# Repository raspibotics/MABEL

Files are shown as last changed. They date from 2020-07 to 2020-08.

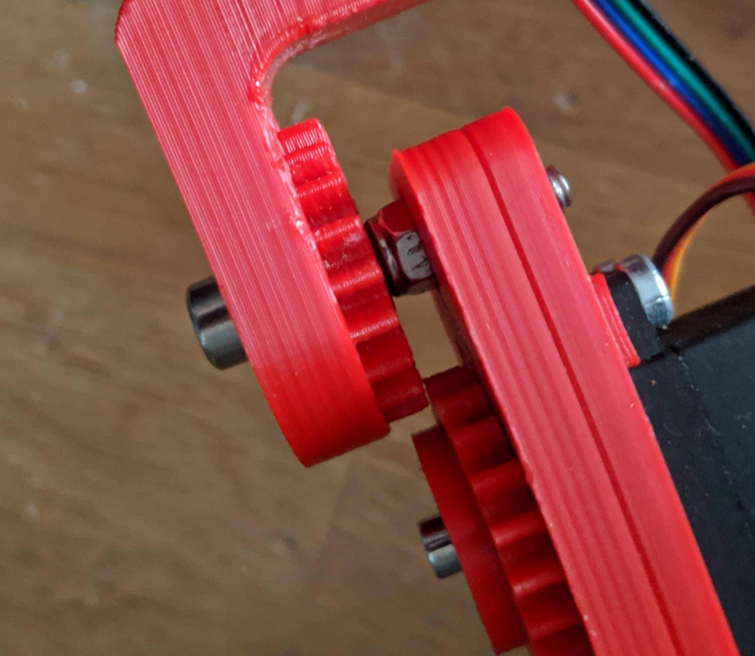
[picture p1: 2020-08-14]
docs/images/Mech_Step_1/Step_1(3).jpeg

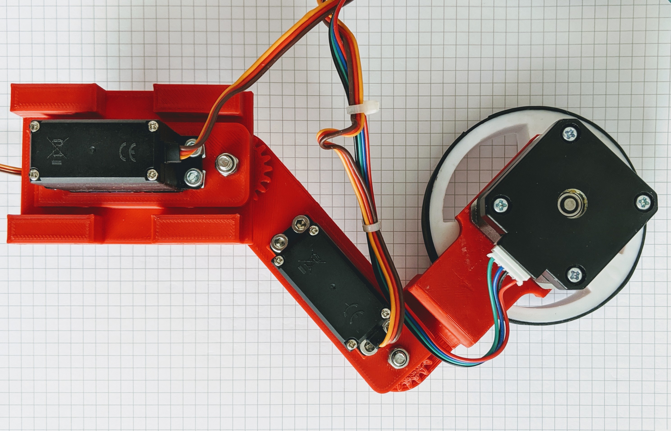
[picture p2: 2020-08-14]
docs/images/Mech_Step_5/Mech_Step_5.jpg

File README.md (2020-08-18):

# MABEL (Multi Axis Balancer Electronically Levelled)
MABEL
## Table of contents
 - [About MABEL](#about-mabel)
   - [Features and design](#features-and-design)
 - [Bill of Materials (BOM)](#bill-of-materials)
   - [3D Printable](#3d-printable)
   - [Non 3D Printable](#non-3d-printable)
     - [Electronic components](#electronic-components)
     - [Mechcanical components](#mechanical-components)
 - [Build instructions](#build-instructions)
     - [Mechanical assembly](#mechanical-assembly)
     - [Electronics assembly](#electronics-assembly)
 - [Installation](#installation)
     - [Dependencies](#required-librariesdependencies)
 - [Usage](#usage)
     - [Inverse kinematics - Moving the legs](#iksolve---inverse-kinematics-for-mabel)
     - [Driving controls and serial communication](#driving-controls)
 - [Contact/Support](#contactsupport)

## About MABEL
**MABEL** is an **ongoing** open source self balancing robot project that is inspired by the famous [Boston Dynamics Handle robot](https://www.youtube.com/watch?v=-7xvqQeoA8c "Boston Dynamics Handle robot"). The robot is controlled via an **Arduino** that handles all of the PID calculations (based off of open source [YABR](http://www.brokking.net/yabr_main.html " YABR") firmware) based on the angle received from an MPU-6050 Accelerometer/Gyro, whilst a **Raspberry pi** (code in **python**) manages Bluetooth and servo control, running an inverse kinematics algorithm to translate the robot legs perfectly in two axes.

> The goal of **MABEL** is to create an affordable legged balancing robot platform like the the Boston Dynamics Handle robot that can built on a hobby scale using cheap Amazon parts and components.

By having a balancing platform with articulated legs **MABEL** will be able to actively balance in multiple Axes and vary leg length depending on the surroundings to increase terrain and off-road performance.

**MABEL** has built on the open source [YABR](http://www.brokking.net/yabr_main.html "YABR") project for the PID controller but with the addition of servos and a pi that helps interface them and control everything.
### Features and design 
Some of the stand-out features that make **MABEL** different from other balancing robots are:
- **Movable Legs** (**Enhanced mobility**, **terrain** and **stabilisation** capabilities)
- **Inverse Kinematics** for each legs that enables accurate translation in (x, y) coordinates using the [IKSolve.py](https://github.com/raspibotics/MABEL/blob/master/raspi_code/IKSolve.py) class
- **Raspberry Pi** enabled (for **Bluetooth control**, **wireless connectivity** and **Computer Vision** capabilities)
- **Common/cheap build materials** (All of the materials can be purchased off of Amazon/Ebay for a low cost)
- **Stepper Motors** (Accurate positioning and precise control)

## Bill of materials
### 3D Printable
3D Printable files are found in [/CAD/3D Models (To Print)](https://github.com/raspibotics/MABEL/tree/master/CAD/3D%20Models%20(To%20print))
- [BatteryPack](https://github.com/raspibotics/MABEL/blob/master/CAD/3D%20Models%20(To%20print)/BatteryPack.stl) (**Optional** - holds LiPo battery onto back of robot with M5 Bolts)
- **2x** [BodyPanel](https://github.com/raspibotics/MABEL/blob/master/CAD/3D%20Models%20(To%20print)/BodyPanel.stl) (Mounting for the 'Hip' servos and side panels of the body)
- [BodyTop](https://github.com/raspibotics/MABEL/blob/master/CAD/3D%20Models%20(To%20print)/BodyTop.stl)
- **4x** [DriverGear](https://github.com/raspibotics/MABEL/blob/master/CAD/3D%20Models%20(To%20print)/DriverGear.stl)
- [Housing](https://github.com/raspibotics/MABEL/blob/master/CAD/3D%20Models%20(To%20print)/Housing.stl) (**LOWER** body housing for MABEL)
- **2x** [LowerLeg](https://github.com/raspibotics/MABEL/blob/master/CAD/3D%20Models%20(To%20print)/LowerLeg.stl)
- **2x** [UpperLeg](https://github.com/raspibotics/MABEL/blob/master/CAD/3D%20Models%20(To%20print)/UpperLeg.stl)
- [PanBracketHead](https://github.com/raspibotics/MABEL/blob/master/CAD/3D%20Models%20(To%20print)/PanBracketHead.stl) (**Optional** Pan servo bracket for head assembly)
- [TiltBracketHead](https://github.com/raspibotics/MABEL/blob/master/CAD/3D%20Models%20(To%20print)/TiltBracketHead.stl) (**Optional** Tilt servo bracket for head assembly)
- [UpperBody](https://github.com/raspibotics/MABEL/blob/master/CAD/3D%20Models%20(To%20print)/UpperBody.stl) (**UPPER** body housing for MABEL)
- **2x** [Wheel](https://github.com/raspibotics/MABEL/blob/master/CAD/3D%20Models%20(To%20print)/Wheel.stl) (**Optional** You can 3D Print your own set of wheels, or buy wheels)

### Non 3D Printable
Here are the Non 3D printable materials to build **MABEL** that **must be either purchased or sourced**. **This includes all of the electronics, mechanical hardware and fixings.** It is **recommended to overbuy the nuts and bolts fixings, as the exact number can change between builds.** This [amazon list](https://www.amazon.co.uk/gp/registry/wishlist/1K7SOU8MRG2K7/ref=cm_wl_huc_view) contains a rough idea of what needs to be purchased.

### Electronic components
- **Raspberry Pi** Zero W
- **PCA9865** Servo Controller (A **PiconZero** could, and previously was used)
- **Variable voltage regulator** (**Optionally** 2x regulator to supply servos with a higher voltage than the 5V required for the  pi)
- **Arduino** Uno 
- **6x** MG996R metal gear servos
- **2x** 38mm NEMA17 stepper motors
- **2x** A4988 (or **DRV8825**) stepper motor drivers 
- Arduino CNC Shield
- MPU-6050 gyro/accelerometer
- 11.1V 2800mAh 3S LiPo (**LiPo battery charger is required**)

### Mechanical components
- **Optional** Grippy rubber material for tyre tread if you are using the [Wheel](https://github.com/raspibotics/MABEL/blob/master/CAD/3D%20Models%20(To%20print)/Wheel.stl) provided.
- **6x** Aluminium servo horns (for **MG996R** servos)
- **8x** 	10mm diameter bearings (5mm internal diameter) x 4mm depth 
- **12x** 10mm M3 bolts
- **12** 15mm M5 bolts
- **4x** 30mm M5 bolts
- **16x** 15mm M4 bolts
- **20x** M5 locknuts and washers

## Build instructions
***UNDER CONSTRUCTION**: This section will include:*
- *Recommended 3D printer settings for 3D Printable parts*
- *Mechanical assembly instructions*
- *Electronics/Wiring instructions*

## Mechanical assembly
---

### **Step 1:** Press the bearings into the joints 
push fit the bearings and secure with a nut and bolt Push fit bearings

 Each leg section ([UpperLeg](https://github.com/raspibotics/MABEL/blob/master/CAD/3D%20Models%20(To%20print)/UpperLeg.stl)  and [LowerLeg](https://github.com/raspibotics/MABEL/blob/master/CAD/3D%20Models%20(To%20print)/LowerLeg.stl)) requires **two bearings (thats 8x bearings in total) to push fit on opposing sides** to ensure smooth rotation. The bearings can be quite tricky to fit so it's **advisable to either apply slow, even pressure with a bench vice**, or to **soften the plastic with a hairdryer** to make it easier to push in by hand. Once you've fitted the bearings, you need to **push an M5 (**4x in total**) (30mm) bolt through** the hole left and **secure with a locknut**.
 [*More reference images for Step 1*](https://github.com/raspibotics/MABEL/tree/master/docs/images/Mech_Step_1)

---

### **Step 2:** Attach **4x** Servos to the [UpperLeg](https://github.com/raspibotics/MABEL/blob/master/CAD/3D%20Models%20(To%20print)/UpperLeg.stl)(s)and [BodyPanel](https://github.com/raspibotics/MABEL/blob/master/CAD/3D%20Models%20(To%20print)/BodyPanel.stl)(s) using **M4 (15mm)** bolts 
Attach servos with M4 bolt Attach servos

**4x MG996R servos** must be secured to **2x BodyPanel and 2x UpperLeg** using **4x M4 (15mm) bolts (16x in total)**. The servos **must sit flat** against these parts with the **shaft facing towards the outside of the robot**. *Your **servos may have a small rib** that you can **easily sand or file off** to get the servo to sit in this orientation.* [*More reference images for Step 2*](https://github.com/raspibotics/MABEL/tree/master/docs/images/Mech_Step_2)

---

### **Step 3:** Push fit and screw the **servo horns** into the [DriverGear](https://github.com/raspibotics/MABEL/blob/master/CAD/3D%20Models%20(To%20print)/DriverGear.stl)(s) and attach the assemblies to the servos 
push fit servo horns and attach gear to servo Assemble DriverGear

Take your **4x DriverGear parts** and **4x Aluminium Servo horns** and push it into the recess on the bottom of the gear. Then **secure the servo horns to each of the gears using the screws** that (should) come with servo horns. Once the gear assembly has been completed, screw it on to the **servo shaft** using **one M3 (10mm) bolt per servo**. [*More reference images for Step 3*](https://github.com/raspibotics/MABEL/tree/master/docs/images/Mech_Step_3)

---

### **Step 4:** Attach the NEMA17 Motors to the [LowerLeg](https://github.com/raspibotics/MABEL/blob/master/CAD/3D%20Models%20(To%20print)/LowerLeg.stl) and fit the wheels
push fit wheels, attach motors Fit wheels and motors

Secure one **NEMA17** (**2x in total**) stepper motor to each of your (**2x**) [LowerLeg](https://github.com/raspibotics/MABEL/blob/master/CAD/3D%20Models%20(To%20print)/LowerLeg.stl) parts with **4x M3 (10mm)** bolts (**8x in total**). Next, prepare your wheels and then **push fit** onto the NEMA17 shafts, **securing if necessary with an M4 bolt**:
- If you are **using the included** [Wheel](https://github.com/raspibotics/MABEL/blob/master/CAD/3D%20Models%20(To%20print)/Wheel.stl) part, you will **need to wrap the outside** in a thin layer of **grippy material** such as **elastic bands** or in my case, **rubber 'O' rings** which help create **traction**.
- If you've **sourced your own wheels**, insert them onto the NEMA17 shafts, and secure as necessary. 

[*More reference images for Step 4*](https://github.com/raspibotics/MABEL/tree/master/docs/images/Mech_Step_4)

---

### **Step 5:** Attach the [LowerLeg](https://github.com/raspibotics/MABEL/blob/master/CAD/3D%20Models%20(To%20print)/LowerLeg.stl), [UpperLeg](https://github.com/raspibotics/MABEL/blob/master/CAD/3D%20Models%20(To%20print)/UpperLeg.stl) and [BodyPanel](https://github.com/raspibotics/MABEL/blob/master/CAD/3D%20Models%20(To%20print)/BodyPanel.stl) assemblies together using **4x M5 locknuts**

Attach all assemblies so far together Fit everything together

Now that you have fitted the BodyPanel and UpperLeg parts with servos (**Step 2**) and gears (**Step 3**), and prepared the UpperLeg and LowerLeg sections with bearings, an M5 bolt and a lock nut each (**Step 1**), you can **insert the UpperLeg section into the BodyPanel** and **secure it with a locknut** on the back (servo) side. Then, **secure the LowerLeg assembly to the UpperLeg** assembly with another **M5 locknut** to form one leg. **This step should then be repeated for the side.** 

**NOTE:** When fitting the parts together, **special attention** should be considered to the **position of the servo rotors**. With standard 180 degree servos, full range of motion is only possible with one way of the legs being bent (The minimum leg height requires a greater than 90 degree angle for example) - **decide which way the legs should bend out** and turn the servo gear manually by hand to **allow a greater range of motion in that direction** than the other (it will be opposite because of the gear drive). You will then **calibrate the servos later on** with a new 0 **position** that's needed for the legs to work properly.

[*More reference images for Step 5*](https://github.com/raspibotics/MABEL/tree/master/docs/images/Mech_Step_5)

---
## Electronics Assembly
***This section will contain instructions about the construction of the robot electronics***

---
## Installation
### Required Libraries/Dependencies
The **MABEL** project relies on multiple open-source and independent libraries, whilst MABELs own classses and functions may run natively, certain libraries are required for full functionality.

- Adafruit ServoKit PCA9865 servo controller library - [Installation guide](https://learn.adafruit.com/adafruit-16-channel-servo-driver-with-raspberry-pi/overview)
- python3 Cwiid (**Optional** - If you want to use a Wiimote controller) - [Installation guide](https://automaticaddison.com/how-to-make-a-remote-controlled-robot-using-raspberry-pi/)
- [approxeng.input](https://approxeng.github.io/approxeng.input/) (**Optional** - If you want to use a different controller - **recommended**)
  
***The controller code is still under development, however the approxeng.input library is recommended to develop controller code with - Versions for both the approxeng.input libary and Cwiid will be released eventually.***

Aftere following the installation instructions for the [ServoKit](https://learn.adafruit.com/adafruit-16-channel-servo-driver-with-raspberry-pi/overview) and controller library of your choice, you should be able to clone to the Raspberry Pi with `git clone https://www.github.com/raspibotics/MABEL`, all controller code, and other scripts should be written in the [MABEL/raspi_code/](https://github.com/raspibotics/MABEL/tree/master/raspi_code) directory so that the code will be able to reference the code already included.

## Usage 
### IKSolve - (Inverse Kinematics for MABEL)
**IKSolve** is the class that handles the **inverse kinematics** functionality for **MABEL** [(IKSolve.py)](https://github.com/raspibotics/MABEL/blob/master/raspi_code/IKSolve.py) and allows for the legs to be translated using **(x, y)** coordinates. It's really simple to use, all that you need to specify are the **home values of each servo** (these are the angles that when passed over to your servos, make the legs point **directly and straight downwards** at **90 degrees**). Keep in mind that the values below are just my servo home positions, and **yours will be different**. 
 
 *The code below is taken directly from [IKDemo.py](https://github.com/raspibotics/MABEL/blob/master/raspi_code/IKDemo.py)*

```python
from IKSolve import IKSolve

# Servo Home Values (degrees) - ***YOURS WILL DIFFER***
# ru_home = 50   # Right leg upper joint home position (servo_angle[0])
# rl_home = 109   # Right leg lower joint home position (servo_angle[1])
# lu_home = 52   # Left leg upper joint home position (servo_angle[2])
# ll_home = 23   # Left leg lower joint home position (servo_angle[3])
 
ik_handler = IKSolve(ru_home=50, rl_home=109,  # Pass home positions to IK class
                     lu_home=52, ll_home=23)  
```
***The class can also be initialised with different leg length segments but these are best left to default unless you have changed the length of any of the leg components.***
```python
def __init__(self, ru_home, rl_home, lu_home,  
                 ll_home, upper_leg=92, lower_leg=75):
```
To recieve suitable angles for each servo to move to (x, y) you must use `translate_xy(self, x, y, flip=False)` (Flip inverts the direction that the legs bend, by default this should be set **False**)

- **x translates the robot leg vertically and y translates the leg horizontally**, each value should be in integer mm
  
 - **x is the distance between the upper leg pivot and wheel centre** (Vertically) - acceptable range for MABEL (160-98mm)
  
 - **y is the distance between the upper leg pivot and wheel centre** (Horizontally) - acceptable range for MABEL (-50, 50mm)
 
```python
  x = int(input('x:'))
  y = int(input('y:'))
  servo_angle = ik_handler.translate_xy(x, y, flip=False) 
  # The angles calculated are stored in a tuple E.g. servo_angles[0-3]
  # You can pass these values to your servo controller code
```
Here are the **mathematical equations** that were calculated for MABELs inverse kinematics, and are expressed in the ```translate_xy()``` function in IKSolve. A is used for calculating angles for the top servos (mounted to the BodyPanel) B is used to calculate angles for the 'Knee' servos. ***Upper*** represents the distance of the **UpperLeg** from pivot to pivot and ***lower*** represents the distance between the **LowerLeg** pivot and centre of the wheel (motor shaft).

<a href="https://github.com/raspibotics/MABEL/blob/master/docs/IKSolve/IKSolveFormulaForA.png" target="_blank">A = Cos^{-1}(\frac{upper^{2}+x^{2}-lower^{2}}{2\cdot upper\cdot x}) + Tan^{-1}(\frac{y}{x})</a>

<a href="https://github.com/raspibotics/MABEL/blob/master/docs/IKSolve/IKSolveFormulaForB.png" target="_blank">B = Cos^{-1}(\frac{upper^{2}+lower^{2}-(x^{2}+y^{2})}{2\cdot upper\cdot lower})</a>
### Driving controls
**MABEL** is designed to work by listening to commands on the Arduino (PID contoller) end that are sent to it by the raspberry pi over serial (using [pySerial](https://pyserial.readthedocs.io/en/latest/)). This allows easy control using bluetooth and web based solutions that are much more difficult to get working on an Arduino. The code snippets below show how you could modify/write your own controller code by sending specific bytes over serial to the arduino and [YABR](http://www.brokking.net/yabr_main.html) based firmware.

In order to use serial commands to drive MABEL around, you first need to find what serial port that the USB connection between the raspberry pi and arduino is called. In my case it was ```/dev/ttyACM0``` but yours could be different. To find what serial port your arduino is connected to, type ```ls /dev/tty*``` into the terminal **without the arduino connected**. Then **reconnect the arduino**, run ```ls /dev/tty*``` again, and make a note of which serial port appears to be listed that was not previously there - **this is your serial port.**

*Once you know what serial port the arduino is connected on, you should initialise the serial class with it:*
```python
import serial
from struct import pack
from time import sleep

ser = serial.Serial(port='/dev/ttyACM0', # ls /dev/tty* to find your port
		baudrate = 9600,
		parity = serial.PARITY_NONE,
		stopbits = serial.STOPBITS_ONE,
		bytesize = serial.EIGHTBITS,
		timeout = 1)
```
The YABR code on the arduino accepts bytes [0, 1, 2, 4, 8] as driving input commands, with **0b00000000 being 'No movement/ remain stationary'**:
```python
# sendByte code
# 00000000 - Do nothing
# 00000001 - Turn left
# 00000010 - Turn right
# 00000100 - Move forwards
# 00001000 - Move backwards
```
We can then send these bytes over the serial connection, and tell **MABEL** in which direction to move - Here's an example of how to write to the arduino serial port, with a bit of **controller pseudocode** for clarity:
```python
while True:
    sendByte |= 0b00000000 
    if controller.direction == 'LEFT': # Controller pseudocode 
        sendByte |= 0b00000001 # This could be any sendByte
    val = pack("B", sendByte)
    ser.write(val) # Send the value over to the arduino 
    sleep(0.04) # Sleep for this period before sending next command
```

## Contact/Support
Thanks for taking an interest in MABEL and its development! If you have any questions or need information whilst building MABEL, please feel free to mention me on twitter [@raspibotics](https://twitter.com/raspibotics) or send me an email at **raspibotics@gmail.com**. ***Whilst this page is still undergoing development, you can find updates and more information on my blog [https://raspibotics.wixsite.com/pibotics-blog](https://raspibotics.wixsite.com/pibotics-blog), where I have been posting about the development of MABEL.***

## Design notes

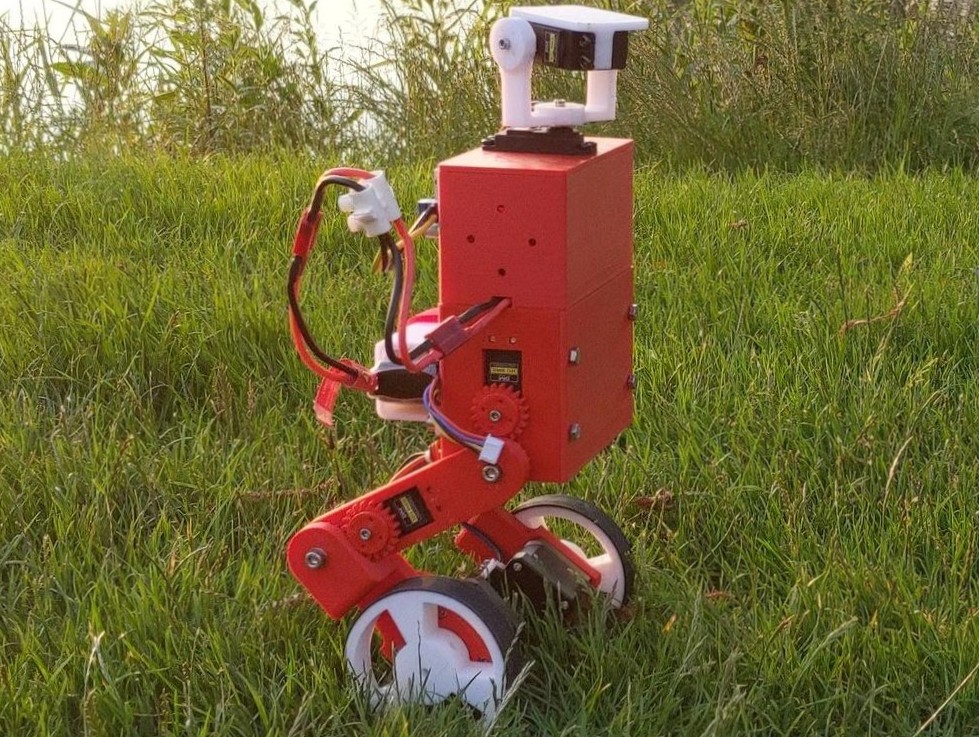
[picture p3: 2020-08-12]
docs/images/MABEL.jpeg

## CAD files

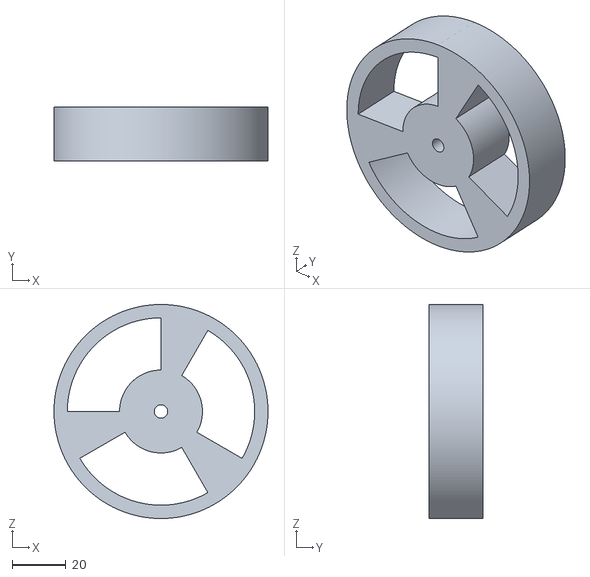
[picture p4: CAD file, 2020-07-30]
CAD/3D Models (To print)/Wheel.stl
80.0 x 20.0 x 80.0

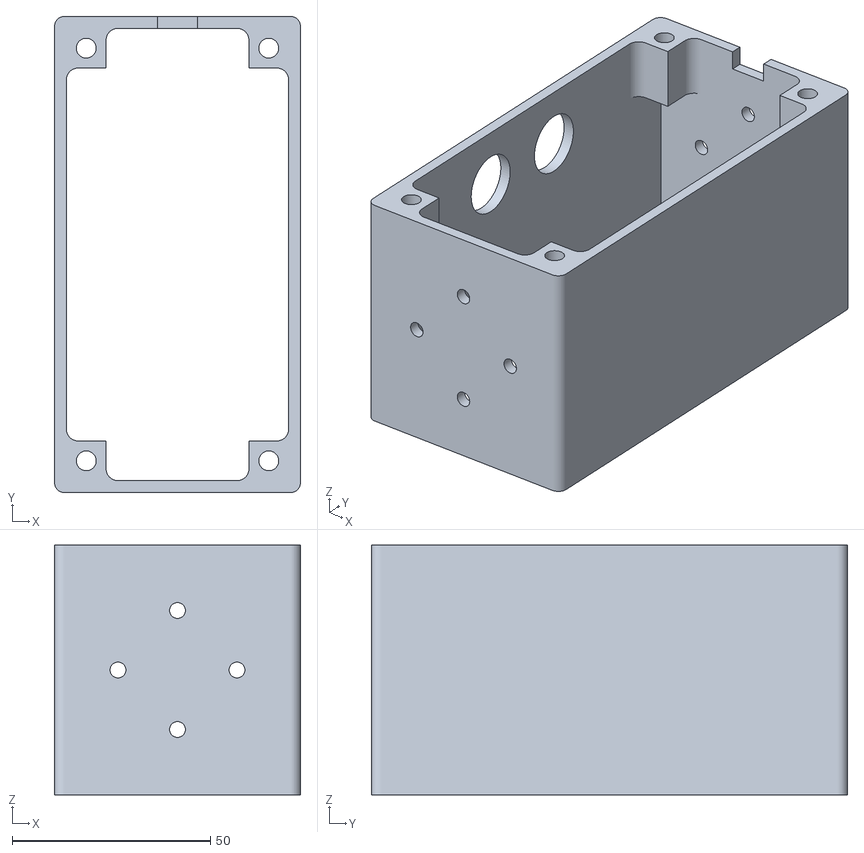
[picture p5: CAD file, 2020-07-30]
CAD/3D Models (To print)/UpperBody.stl
62.0 x 120.0 x 63.0

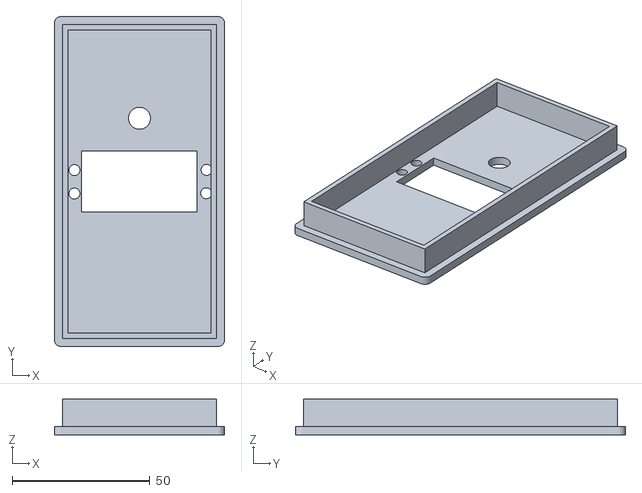
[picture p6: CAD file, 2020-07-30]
CAD/3D Models (To print)/BodyTop.stl
62.0 x 120.0 x 13.0

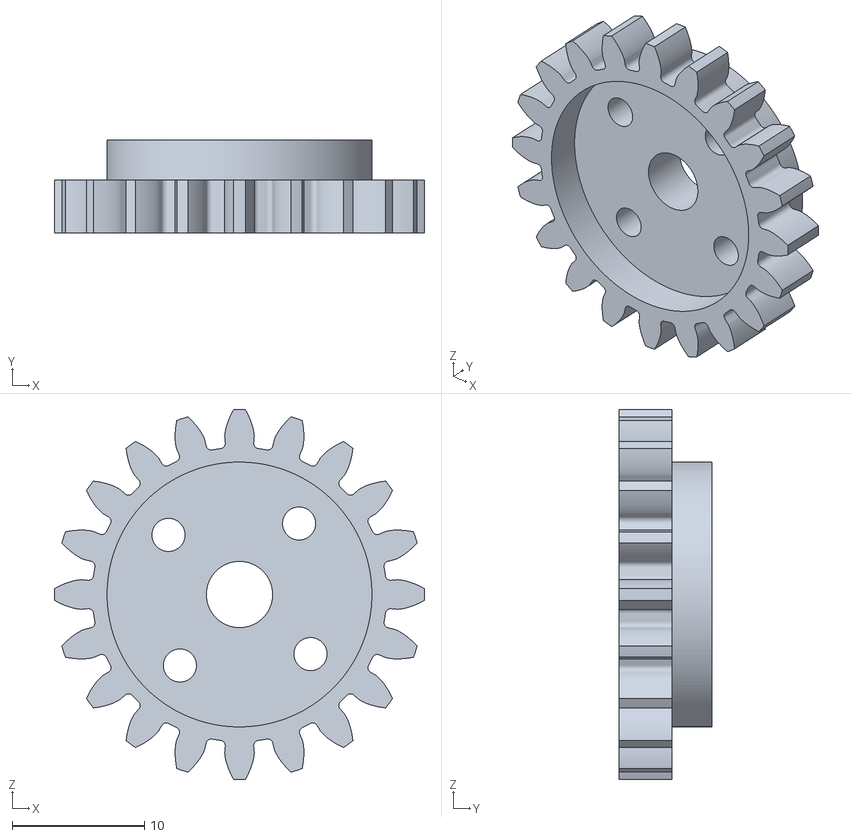
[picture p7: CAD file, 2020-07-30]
CAD/3D Models (To print)/DriverGear.stl
27.9 x 7.00 x 27.9

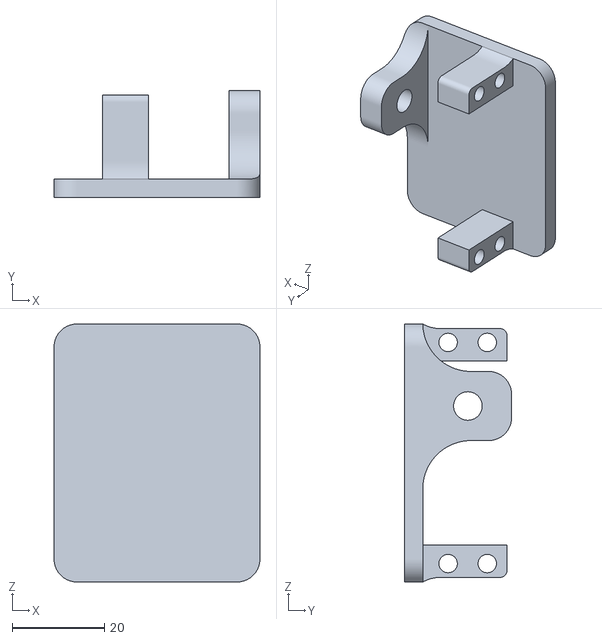
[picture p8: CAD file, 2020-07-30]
CAD/3D Models (To print)/TiltBracketHead.stl
44.7 x 23.3 x 56.0

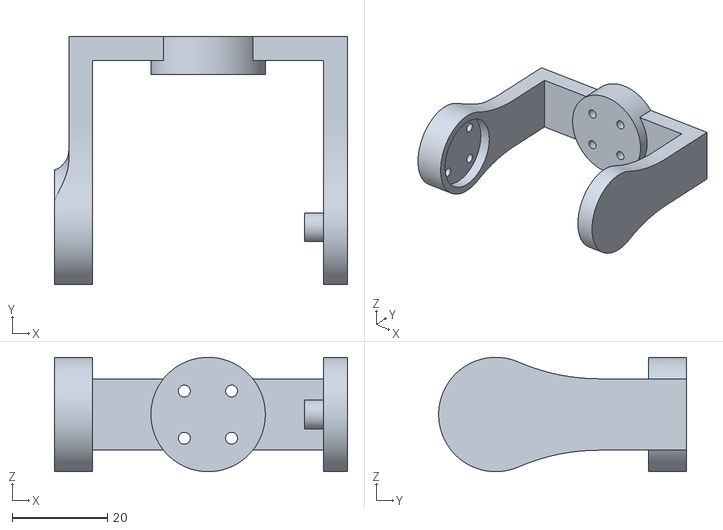
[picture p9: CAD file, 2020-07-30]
CAD/3D Models (To print)/PanBracketHead.stl
61.5 x 52.0 x 24.0

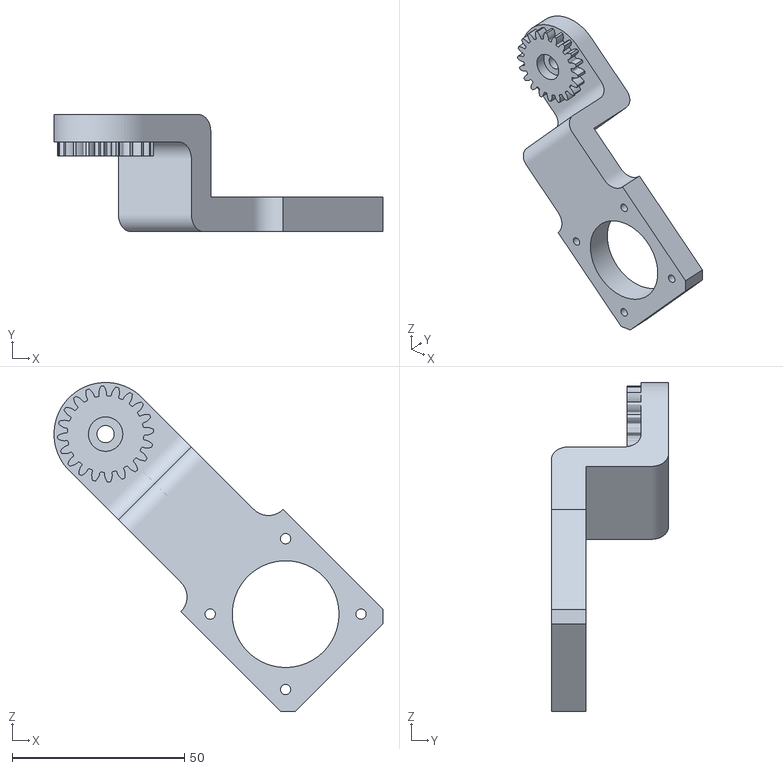
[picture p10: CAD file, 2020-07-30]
CAD/3D Models (To print)/LowerLeg.stl
95.6 x 34.0 x 95.6

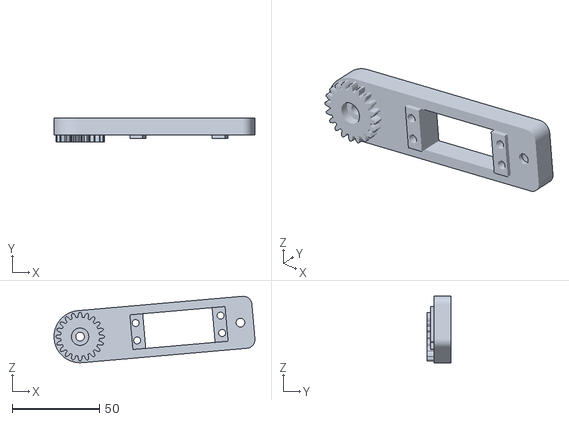
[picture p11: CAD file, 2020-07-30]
CAD/3D Models (To print)/UpperLeg.stl
115.5 x 14.0 x 38.2

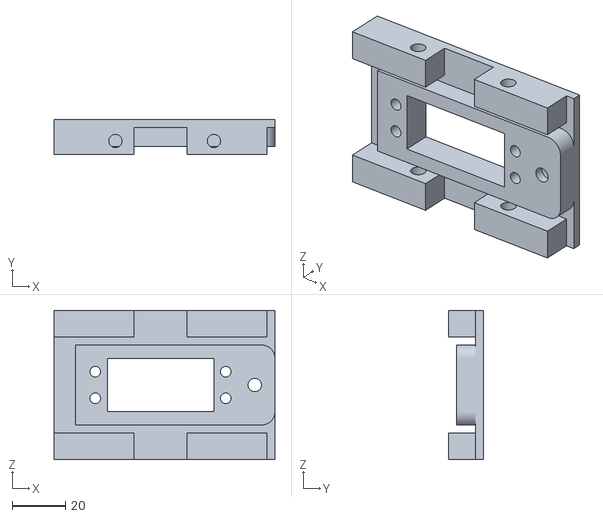
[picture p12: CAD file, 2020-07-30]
CAD/3D Models (To print)/BodyPanel.stl
83.0 x 13.0 x 56.0

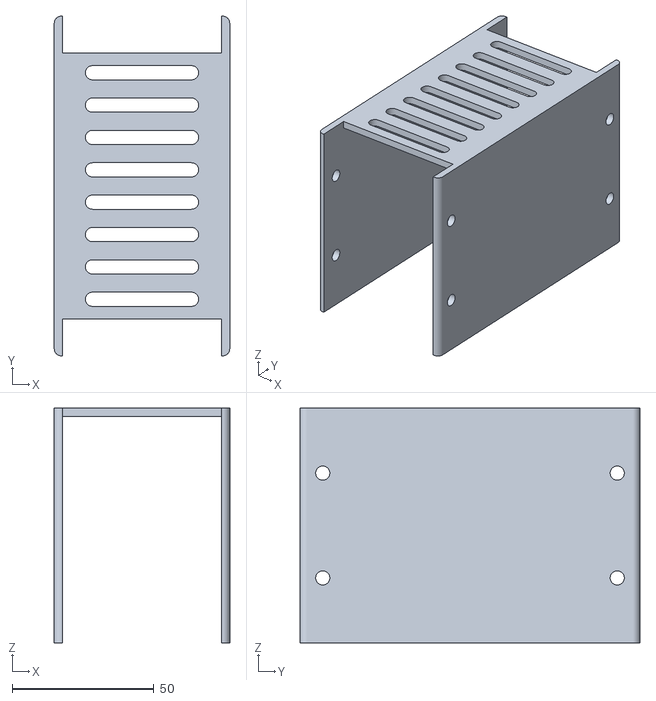
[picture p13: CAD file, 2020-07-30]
CAD/3D Models (To print)/Housing.stl
62.0 x 120.0 x 83.0

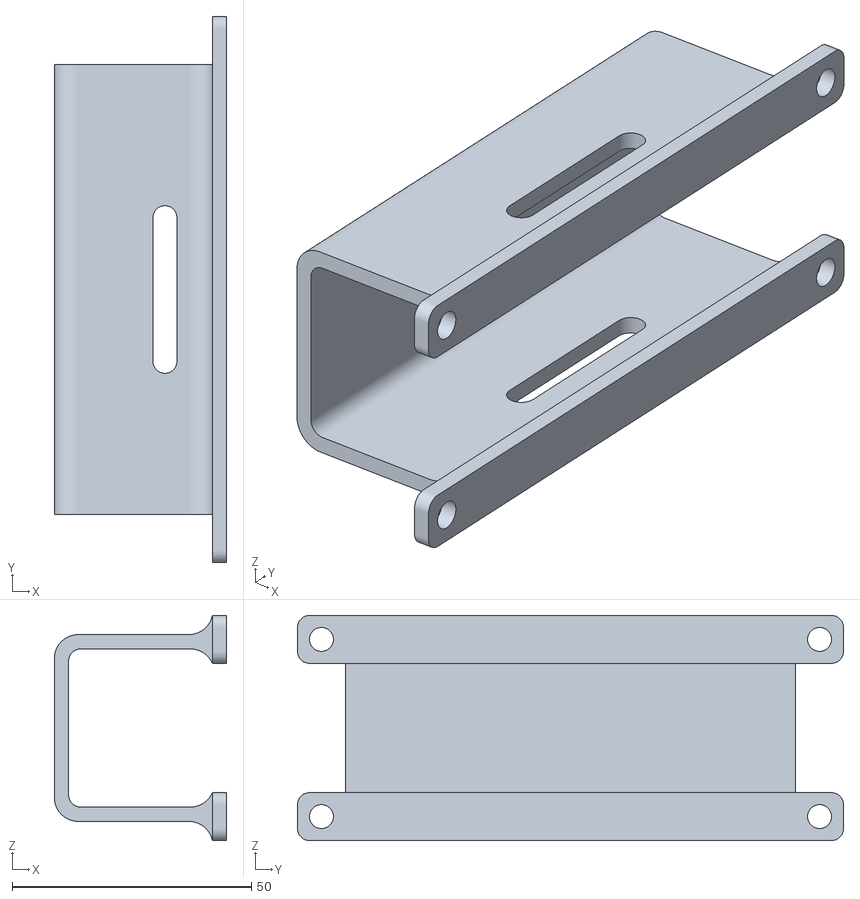
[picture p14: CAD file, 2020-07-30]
CAD/3D Models (To print)/BatteryPack.stl
36.0 x 114.0 x 47.0

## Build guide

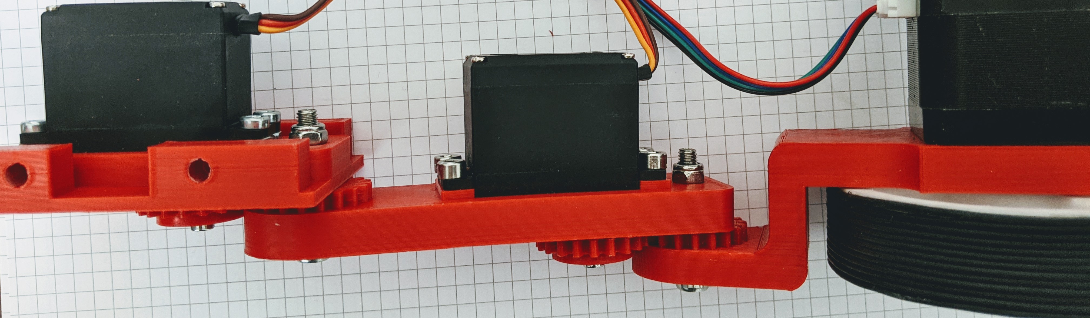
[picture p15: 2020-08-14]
docs/images/Mech_Step_5/Mech_Step_5_side_view.jpg

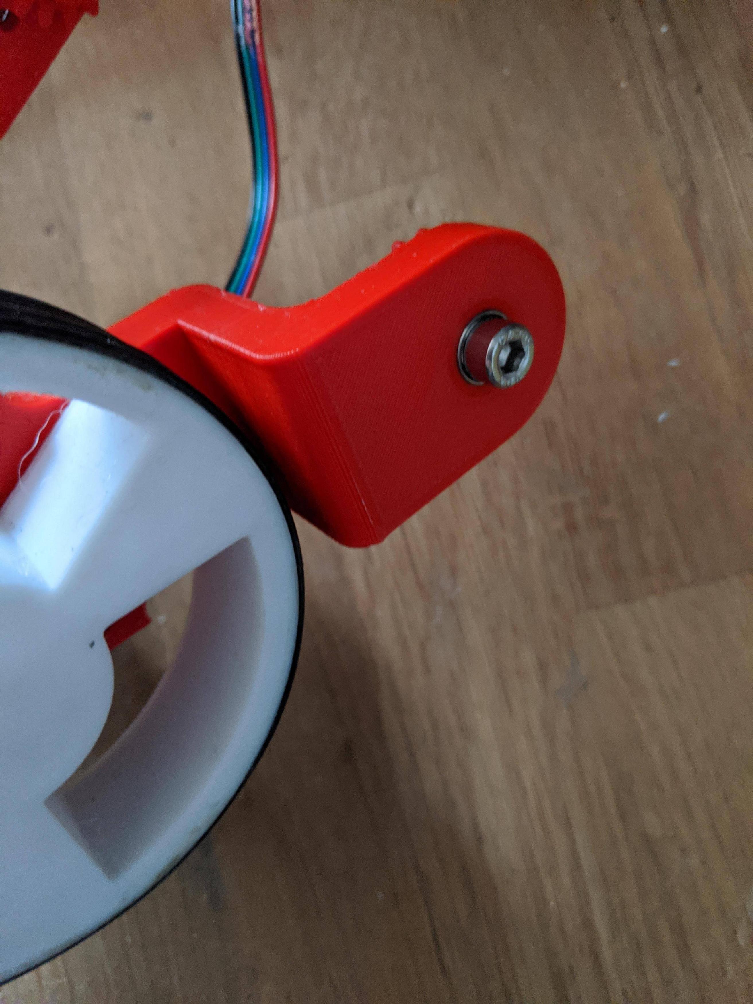
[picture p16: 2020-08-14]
docs/images/Mech_Step_1/Step_1(2).jpeg

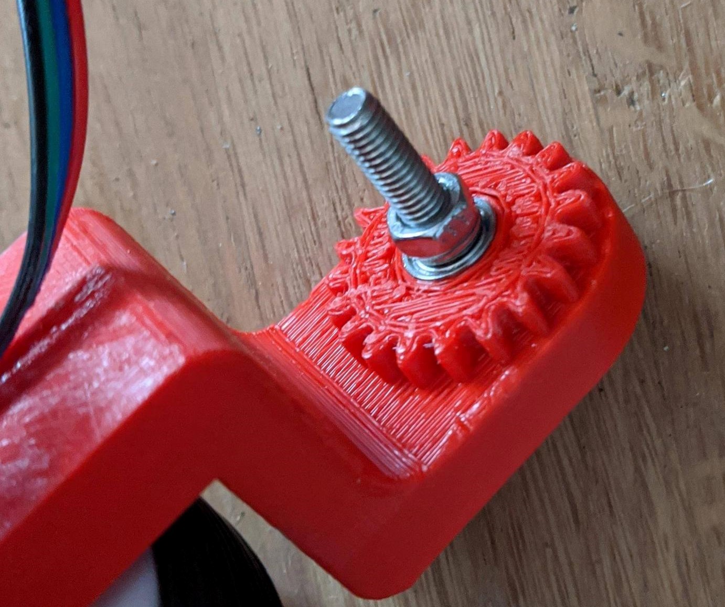
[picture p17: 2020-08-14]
docs/images/Mech_Step_1/Step_1(1).jpeg

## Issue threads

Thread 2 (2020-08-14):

Typo in parts list?

carlkesselman, 2020-08-14:
Hi,

I think there may be a type in the parts list: PCA9865 -> PCA9685?

It's a bit confusing as it seems you have changed from the Picon Zero to this alternative, which I assume will still be controlled from the Pi, not the Arduino?

Carl

raspibotics, 2020-08-14:
Hi,
I've recently switched over to the PCA9865 servo controller on the pi as it's cheaper and more suited to my robot application, although a Piconzero is still a valid servo controller for the Pi.

raspibotics, 2020-08-15:
Updated parts list with (PiconZero could, and previously was used)

Closed 2020-08-15.

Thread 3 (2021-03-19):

Can't get YABR code running on Arduino Uno + CNC Shield

ghost, 2021-03-19:
Hey there,
I'm having some issues getting the YABR code working. I've got the same hardware as mentioned in your project. An Arduino Uno (SMD version, should not differ, as far as I researched) and CNC Shield. It seems the code fails on following line:
`TIMSK2 |= (1 << OCIE2A);`
The result of running the YABR code are two non functional stepper motors. One of them can be moved by hand, the other one being blocked at a position. Both are producing some noise. I checked the current limit on the driver and used other motor drivers. Unfortunately without success.

I tried to increase `OCR2A = 39;` to `3999999` which should result in a timer interrupt every 2 seconds instead the 20 µs, but looking into serial output the timer would still spam the code, way faster than 2 seconds.
I replaced the Arduino with another one (different brand, same processor, not SMD). Same behavior there.
I replaced the writing to `PORTD` with `digitalWrite()` but had no luck either.

Could it be possible that I'm missing out on some point not mentioned in the guide?

Greetings,
Niko

raspibotics, 2021-03-19:
Hi Niko,

I had issues at first with getting my steppers to cooperate. I would
suggest testing some seperate example code to see if you can get any sort
of movement out. Are you absolutely sure that you've wired the correct
stepper coils to the stepper drivers? I know when I did the guide I was
following had some inaccuracies so I had to use trial and error as well as
measuring the resistance to determine which order the coils should be
connected. If they are connected wrong the stepper will move unexpectedly
or lock up but when working correctly should activate when the
accelerometer reads the critical value.

There shouldn't be too many differences with board pinnout and I'm afraid I
can't help diagnose too many software issues with the original YABR code as
I left it mostly unchanged and did most of the software on the raspberry
pi. Although the original author goes through the code in great detail in
these two videos if you rule out hardware.

https://youtu.be/VxpMWncBKZc

https://youtu.be/mG4OtAiY_wU

Hope this helps,

Harry

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

niko-kl, 2021-03-21:
Hi Harry,

thanks for your fast response.
I forgot to mention that I succeeded in controlling the stepper motor with some separate test code, before I asked my first question.
After watching the two videos you linked I noticed that my driver was set to full instead of 1/4 step mode. Setting the jumper my robot started balancing or at least trying it. So the wheels are spinning now, but way to fast.. resulting in the robot falling over. When tilting the robot I can confirm that the wheels are changing their direction, but they are still spinning, even if I balance the robot manually by hand. Did you experience something similar?
Did also correct my MPU position to being equal to the balancing robot in the video. So I can exclude this being a part of the problem.

Current connections on the CNC board are:

- drivers, stepper motor, 1/4 step jumpers
- EN/GND jumper to enable the board
- power input for stepper motor
- MPU connection with SDA/SCL

Am I missing some jumpers?

Greetings,
Niko

raspibotics, 2021-03-21:
Hi!

When oriented like the original the MPU calibration value should be around
1000, once I had sorted out hardware issues the thing balanced pretty well
with no modifications to the PID values. My microstepping jumper is in the
second slot  to create a 1/4 step but where you place the jumper will
differ depending on the truth table for your particular driver. Are you
using A4988 drivers?

Could you send a video, it may help to see what's going on?  The wheels do
spin very fast in mid air but when angled slowly into position it should
just take over and begin balancing.

Harry

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

niko-kl, 2021-03-21:
Hey,

yes I'm using the A4988 driver, so my microstepping jumper is also set on the second slot.
Meanwhile I was able to find my problem. The stepper coils were indeed wired wrong. Fixing that the balancing part finally works.

I made still a [video](https://drive.google.com/file/d/13ucOEg1BF7VQoPmIf4q2sNA6-ISzJRO4/view?usp=sharing) for the (new) sound my stepper motors are producing when I'm lifting the robot. My best guess would be that the current limitation is set wrong. By looking into the datasheet, I read a motor needs 1.7A. So Vref on the driver should be half of that. But neither 0.85V nor less than tha (down to 0.5V) would fix this. Other than that I'd need to get another power adapter, since mine has 12V and only 2.5A, so I can exclude that as an issue.

Niko

raspibotics, 2021-03-21:
Hi!

Wow that's awesome, the Motors have a tendency to do that when they've
stalled, if you increase the motor current allowed this should solve that
although it will still stall in extreme cases, only thing you can do is to
tip the robot on its side which will reset the motors.  By the way us
mentioned setting the VREF to 0.85v for 1.7A, this would be correct for
DRV8825 drivers but for A4988 the formula used is slightly different and is
based on one of the SMD resistors.  This guide should help you set the
correct Vref but it may still stall in extreme cases.

https://e3d-online.dozuki.com/Guide/VREF+adjustment+A4988/92

Harry

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

niko-kl, 2021-03-24:
Hey there,

I guess I have the Stepstick or a clone driver since it's red colored. There is not datasheet available where I bought it.
Taking the information for Rs = 0,2 out of [here](https://v6zmvq5nk5.codesandbox.io/) and input there 1.7A as rated current I get 2.18V for Vref.. which is probably way to high and wrong. I tried to adjust the driver current to 1V and the motor began to get small pulses in idle, so I stopped there.
Adjusted the current just by trial and error and the best value for me seems to be around 0.4 to 0.5 for Vref. Then the motor doesn't even make any sounds in idle. I guess I stick to that solution for the beginning.

raspibotics, 2021-03-24:
Hi,

Yeah it's not a major issue, 1.7A does seem quite high however. I got
confused with stepper powering early on, the current drawn is dependent on
the voltage supplied to the motors, the motor datasheets tend to give a
high rated current but it will usually be at a low supply voltage maybe
around 3V. Since you're powering off I'm assuming around 12V the actual
current should be much lower and the driver current rating should match
that. So looking at rated power may be a more useful metric. Trial and
error will probably work though and you can always increase it later.

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

Closed 2023-09-21.

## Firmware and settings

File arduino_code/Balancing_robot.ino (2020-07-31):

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
#include <Wire.h>                                            //Include the Wire.h library so we can communicate with the gyro

int gyro_address = 0x68;                                     //MPU-6050 I2C address (0x68 or 0x69)
int acc_calibration_value = 1001
;                            //Enter the accelerometer calibration value

//Various settings
float pid_p_gain = 15;                                       //Gain setting for the P-controller (15)
float pid_i_gain = 1.5;                                      //Gain setting for the I-controller (1.5)
float pid_d_gain = 30;                                       //Gain setting for the D-controller (30)
float turning_speed = 30;                                    //Turning speed (20)
float max_target_speed = 150;                                //Max target speed (100)

///////////////////////////////////////////////////////////////////////////////////////////////////////////////////////////////////////
//Declaring global variables
///////////////////////////////////////////////////////////////////////////////////////////////////////////////////////////////////////
byte start, received_byte, low_bat;

int left_motor, throttle_left_motor, throttle_counter_left_motor, throttle_left_motor_memory;
int right_motor, throttle_right_motor, throttle_counter_right_motor, throttle_right_motor_memory;
int battery_voltage;
int receive_counter;
int gyro_pitch_data_raw, gyro_yaw_data_raw, accelerometer_data_raw;

long gyro_yaw_calibration_value, gyro_pitch_calibration_value;

unsigned long loop_timer;

float angle_gyro, angle_acc, angle, self_balance_pid_setpoint;
float pid_error_temp, pid_i_mem, pid_setpoint, gyro_input, pid_output, pid_last_d_error;
float pid_output_left, pid_output_right;
///////////////////////////////////////////////////////////////////////////////////////////////////////////////////////////////////////
//Setup basic functions
///////////////////////////////////////////////////////////////////////////////////////////////////////////////////////////////////////
void setup(){
  Serial.begin(9600);                                                       //Start the serial port at 9600 kbps
  Wire.begin();                                                             //Start the I2C bus as master
  TWBR = 12;                                                                //Set the I2C clock speed to 400kHz

  //To create a variable pulse for controlling the stepper motors a timer is created that will execute a piece of code (subroutine) every 20us
  //This subroutine is called TIMER2_COMPA_vect
  TCCR2A = 0;                                                               //Make sure that the TCCR2A register is set to zero
  TCCR2B = 0;                                                               //Make sure that the TCCR2A register is set to zero
  TIMSK2 |= (1 << OCIE2A);                                                  //Set the interupt enable bit OCIE2A in the TIMSK2 register
  TCCR2B |= (1 << CS21);                                                    //Set the CS21 bit in the TCCRB register to set the prescaler to 8
  OCR2A = 39;                                                               //The compare register is set to 39 => 20us / (1s / (16.000.000MHz / 8)) - 1
  TCCR2A |= (1 << WGM21);                                                   //Set counter 2 to CTC (clear timer on compare) mode
  
  //By default the MPU-6050 sleeps. So we have to wake it up.
  Wire.beginTransmission(gyro_address);                                     //Start communication with the address found during search.
  Wire.write(0x6B);                                                         //We want to write to the PWR_MGMT_1 register (6B hex)
  Wire.write(0x00);                                                         //Set the register bits as 00000000 to activate the gyro
  Wire.endTransmission();                                                   //End the transmission with the gyro.
  //Set the full scale of the gyro to +/- 250 degrees per second
  Wire.beginTransmission(gyro_address);                                     //Start communication with the address found during search.
  Wire.write(0x1B);                                                         //We want to write to the GYRO_CONFIG register (1B hex)
  Wire.write(0x00);                                                         //Set the register bits as 00000000 (250dps full scale)
  Wire.endTransmission();                                                   //End the transmission with the gyro
  //Set the full scale of the accelerometer to +/- 4g.
  Wire.beginTransmission(gyro_address);                                     //Start communication with the address found during search.
  Wire.write(0x1C);                                                         //We want to write to the ACCEL_CONFIG register (1A hex)
  Wire.write(0x08);                                                         //Set the register bits as 00001000 (+/- 4g full scale range)
  Wire.endTransmission();                                                   //End the transmission with the gyro
  //Set some filtering to improve the raw data.
  Wire.beginTransmission(gyro_address);                                     //Start communication with the address found during search
  Wire.write(0x1A);                                                         //We want to write to the CONFIG register (1A hex)
  Wire.write(0x03);                                                         //Set the register bits as 00000011 (Set Digital Low Pass Filter to ~43Hz)
  Wire.endTransmission();                                                   //End the transmission with the gyro 

  pinMode(2, OUTPUT);                                                       //Configure digital poort 2 as output
  pinMode(3, OUTPUT);                                                       //Configure digital poort 3 as output
  pinMode(6, OUTPUT);                                                       //Configure digital poort 4 as output
  pinMode(5, OUTPUT);                                                       //Configure digital poort 5 as output
  pinMode(13, OUTPUT);                                                      //Configure digital poort 6 as output

  
  for(receive_counter = 0; receive_counter < 500; receive_counter++){       //Create 500 loops
    if(receive_counter % 15 == 0)digitalWrite(13, !digitalRead(13));        //Change the state of the LED every 15 loops to make the LED blink fast
    Wire.beginTransmission(gyro_address);                                   //Start communication with the gyro
    Wire.write(0x43);                                                       //Start reading the Who_am_I register 75h
    Wire.endTransmission();                                                 //End the transmission
    Wire.requestFrom(gyro_address, 4);                                      //Request 2 bytes from the gyro
    gyro_yaw_calibration_value += Wire.read()<<8|Wire.read();               //Combine the two bytes to make one integer
    gyro_pitch_calibration_value += Wire.read()<<8|Wire.read();             //Combine the two bytes to make one integer
    delayMicroseconds(3700);                                                //Wait for 3700 microseconds to simulate the main program loop time
  }
  gyro_pitch_calibration_value /= 500;                                      //Divide the total value by 500 to get the avarage gyro offset
  gyro_yaw_calibration_value /= 500;                                        //Divide the total value by 500 to get the avarage gyro offset

  loop_timer = micros() + 4000;                                             //Set the loop_timer variable at the next end loop time

}

///////////////////////////////////////////////////////////////////////////////////////////////////////////////////////////////////////
//Main program loop
///////////////////////////////////////////////////////////////////////////////////////////////////////////////////////////////////////
void loop(){
  if(Serial.available()){                                                   //If there is serial data available
    received_byte = Serial.read();                                          //Load the received serial data in the received_byte variable
    receive_counter = 0;                                                    //Reset the receive_counter variable
  }
  if(receive_counter <= 25)receive_counter ++;                              //The received byte will be valid for 25 program loops (100 milliseconds)
  else received_byte = 0x00;                                                //After 100 milliseconds the received byte is deleted
  
  //Load the battery voltage to the battery_voltage variable.
  //85 is the voltage compensation for the diode.
  //Resistor voltage divider => (3.3k + 3.3k)/2.2k = 2.5
  //12.5V equals ~5V @ Analog 0.
  //12.5V equals 1023 analogRead(0).
  //1250 / 1023 = 1.222.
  //The variable battery_voltage holds 1050 if the battery voltage is 10.5V.
  battery_voltage = (analogRead(0) * 1.222) + 85;
  
  if(battery_voltage < 1050 && battery_voltage > 800){                      //If batteryvoltage is below 10.5V and higher than 8.0V
    digitalWrite(13, HIGH);                                                 //Turn on the led if battery voltage is to low
    low_bat = 1;                                                            //Set the low_bat variable to 1
  }

  ///////////////////////////////////////////////////////////////////////////////////////////////////////////////////////////////////////
  //Angle calculations
  ///////////////////////////////////////////////////////////////////////////////////////////////////////////////////////////////////////
  Wire.beginTransmission(gyro_address);                                     //Start communication with the gyro
  Wire.write(0x3F);                                                         //Start reading at register 3F
  Wire.endTransmission();                                                   //End the transmission
  Wire.requestFrom(gyro_address, 2);                                        //Request 2 bytes from the gyro
  accelerometer_data_raw = Wire.read()<<8|Wire.read();                      //Combine the two bytes to make one integer
  accelerometer_data_raw += acc_calibration_value;                          //Add the accelerometer calibration value
  if(accelerometer_data_raw > 8200)accelerometer_data_raw = 8200;           //Prevent division by zero by limiting the acc data to +/-8200;
  if(accelerometer_data_raw < -8200)accelerometer_data_raw = -8200;         //Prevent division by zero by limiting the acc data to +/-8200;

  angle_acc = asin((float)accelerometer_data_raw/8200.0)* 57.296;           //Calculate the current angle according to the accelerometer

  if(start == 0 && angle_acc > -0.5&& angle_acc < 0.5){                     //If the accelerometer angle is almost 0
    angle_gyro = angle_acc;                                                 //Load the accelerometer angle in the angle_gyro variable
    start = 1;                                                              //Set the start variable to start the PID controller
  }
  
  Wire.beginTransmission(gyro_address);                                     //Start communication with the gyro
  Wire.write(0x43);                                                         //Start reading at register 43
  Wire.endTransmission();                                                   //End the transmission
  Wire.requestFrom(gyro_address, 4);                                        //Request 4 bytes from the gyro
  gyro_yaw_data_raw = Wire.read()<<8|Wire.read();                           //Combine the two bytes to make one integer
  gyro_pitch_data_raw = Wire.read()<<8|Wire.read();                         //Combine the two bytes to make one integer
  
  gyro_pitch_data_raw -= gyro_pitch_calibration_value;                      //Add the gyro calibration value
  angle_gyro += gyro_pitch_data_raw * 0.000031;                             //Calculate the traveled during this loop angle and add this to the angle_gyro variable
  
  ///////////////////////////////////////////////////////////////////////////////////////////////////////////////////////////////////////
  //MPU-6050 offset compensation
  ///////////////////////////////////////////////////////////////////////////////////////////////////////////////////////////////////////
  //Not every gyro is mounted 100% level with the axis of the robot. This can be cause by misalignments during manufacturing of the breakout board. 
  //As a result the robot will not rotate at the exact same spot and start to make larger and larger circles.
  //To compensate for this behavior a VERY SMALL angle compensation is needed when the robot is rotating.
  //Try 0.0000003 or -0.0000003 first to see if there is any improvement.

  gyro_yaw_data_raw -= gyro_yaw_calibration_value;                          //Add the gyro calibration value
  //Uncomment the following line to make the compensation active
  //angle_gyro -= gyro_yaw_data_raw * 0.0000003;                            //Compensate the gyro offset when the robot is rotating

  angle_gyro = angle_gyro * 0.9996 + angle_acc * 0.0004;                    //Correct the drift of the gyro angle with the accelerometer angle

  ///////////////////////////////////////////////////////////////////////////////////////////////////////////////////////////////////////
  //PID controller calculations
  ///////////////////////////////////////////////////////////////////////////////////////////////////////////////////////////////////////
  //The balancing robot is angle driven. First the difference between the desired angel (setpoint) and actual angle (process value)
  //is calculated. The self_balance_pid_setpoint variable is automatically changed to make sure that the robot stays balanced all the time.
  //The (pid_setpoint - pid_output * 0.015) part functions as a brake function.
  pid_error_temp = angle_gyro - self_balance_pid_setpoint - pid_setpoint;
  if(pid_output > 10 || pid_output < -10)pid_error_temp += pid_output * 0.015 ;

  pid_i_mem += pid_i_gain * pid_error_temp;                                 //Calculate the I-controller value and add it to the pid_i_mem variable
  if(pid_i_mem > 400)pid_i_mem = 400;                                       //Limit the I-controller to the maximum controller output
  else if(pid_i_mem < -400)pid_i_mem = -400;
  //Calculate the PID output value
  pid_output = pid_p_gain * pid_error_temp + pid_i_mem + pid_d_gain * (pid_error_temp - pid_last_d_error);
  if(pid_output > 400)pid_output = 400;                                     //Limit the PI-controller to the maximum controller output
  else if(pid_output < -400)pid_output = -400;

  pid_last_d_error = pid_error_temp;                                        //Store the error for the next loop

  if(pid_output < 5 && pid_output > -5)pid_output = 0;                      //Create a dead-band to stop the motors when the robot is balanced

  if(angle_gyro > 30 || angle_gyro < -30 || start == 0 || low_bat == 1){    //If the robot tips over or the start variable is zero or the battery is empty
    pid_output = 0;                                                         //Set the PID controller output to 0 so the motors stop moving
    pid_i_mem = 0;                                                          //Reset the I-controller memory
    start = 0;                                                              //Set the start variable to 0
    self_balance_pid_setpoint = 0;                                          //Reset the self_balance_pid_setpoint variable
  }

  ///////////////////////////////////////////////////////////////////////////////////////////////////////////////////////////////////////
  //Control calculations
  ///////////////////////////////////////////////////////////////////////////////////////////////////////////////////////////////////////
  pid_output_left = pid_output;                                             //Copy the controller output to the pid_output_left variable for the left motor
  pid_output_right = pid_output;                                            //Copy the controller output to the pid_output_right variable for the right motor

  if(received_byte & B00000001){                                            //If the first bit of the receive byte is set change the left and right variable to turn the robot to the left
    pid_output_left += turning_speed;                                       //Increase the left motor speed
    pid_output_right -= turning_speed;                                      //Decrease the right motor speed
  }
  if(received_byte & B00000010){                                            //If the second bit of the receive byte is set change the left and right variable to turn the robot to the right
    pid_output_left -= turning_speed;                                       //Decrease the left motor speed
    pid_output_right += turning_speed;                                      //Increase the right motor speed
  }

  if(received_byte & B00000100){                                            //If the third bit of the receive byte is set change the left and right variable to turn the robot to the right
    if(pid_setpoint > -2.5)pid_setpoint -= 0.05;                            //Slowly change the setpoint angle so the robot starts leaning forewards
    if(pid_output > max_target_speed * -1)pid_setpoint -= 0.005;            //Slowly change the setpoint angle so the robot starts leaning forewards
  }
  if(received_byte & B00001000){                                            //If the forth bit of the receive byte is set change the left and right variable to turn the robot to the right
    if(pid_setpoint < 2.5)pid_setpoint += 0.05;                             //Slowly change the setpoint angle so the robot starts leaning backwards
    if(pid_output < max_target_speed)pid_setpoint += 0.005;                 //Slowly change the setpoint angle so the robot starts leaning backwards
  }   

  if(!(received_byte & B00001100)){                                         //Slowly reduce the setpoint to zero if no foreward or backward command is given
    if(pid_setpoint > 0.5)pid_setpoint -=0.05;                              //If the PID setpoint is larger then 0.5 reduce the setpoint with 0.05 every loop
    else if(pid_setpoint < -0.5)pid_setpoint +=0.05;                        //If the PID setpoint is smaller then -0.5 increase the setpoint with 0.05 every loop
    else pid_setpoint = 0;                                                  //If the PID setpoint is smaller then 0.5 or larger then -0.5 set the setpoint to 0
  }
  
  //The self balancing point is adjusted when there is not forward or backwards movement from the transmitter. This way the robot will always find it's balancing point
  if(pid_setpoint == 0){                                                    //If the setpoint is zero degrees
    if(pid_output < 0)self_balance_pid_setpoint += 0.0015;                  //Increase the self_balance_pid_setpoint if the robot is still moving forewards
    if(pid_output > 0)self_balance_pid_setpoint -= 0.0015;                  //Decrease the self_balance_pid_setpoint if the robot is still moving backwards
  }

  ///////////////////////////////////////////////////////////////////////////////////////////////////////////////////////////////////////
  //Motor pulse calculations
  ///////////////////////////////////////////////////////////////////////////////////////////////////////////////////////////////////////
  //To compensate for the non-linear behaviour of the stepper motors the folowing calculations are needed to get a linear speed behaviour.
  if(pid_output_left > 0)pid_output_left = 405 - (1/(pid_output_left + 9)) * 5500;
  else if(pid_output_left < 0)pid_output_left = -405 - (1/(pid_output_left - 9)) * 5500;

  if(pid_output_right > 0)pid_output_right = 405 - (1/(pid_output_right + 9)) * 5500;
  else if(pid_output_right < 0)pid_output_right = -405 - (1/(pid_output_right - 9)) * 5500;

  //Calculate the needed pulse time for the left and right stepper motor controllers
  if(pid_output_left > 0)left_motor = 400 - pid_output_left;
  else if(pid_output_left < 0)left_motor = -400 - pid_output_left;
  else left_motor = 0;

  if(pid_output_right > 0)right_motor = 400 - pid_output_right;
  else if(pid_output_right < 0)right_motor = -400 - pid_output_right;
  else right_motor = 0;

  //Copy the pulse time to the throttle variables so the interrupt subroutine can use them
  throttle_left_motor = left_motor;
  throttle_right_motor = right_motor;

  ///////////////////////////////////////////////////////////////////////////////////////////////////////////////////////////////////////
  //Loop time timer
  ///////////////////////////////////////////////////////////////////////////////////////////////////////////////////////////////////////
  //The angle calculations are tuned for a loop time of 4 milliseconds. To make sure every loop is exactly 4 milliseconds a wait loop
  //is created by setting the loop_timer variable to +4000 microseconds every loop.
  while(loop_timer > micros());
  loop_timer += 4000;
}
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

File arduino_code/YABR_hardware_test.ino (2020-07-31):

///////////////////////////////////////////////////////////////////////////////////////
//Terms of use
///////////////////////////////////////////////////////////////////////////////////////
//THE SOFTWARE IS PROVIDED "AS IS", WITHOUT WARRANTY OF ANY KIND, EXPRESS OR
//IMPLIED, INCLUDING BUT NOT LIMITED TO THE WARRANTIES OF MERCHANTABILITY,
//FITNESS FOR A PARTICULAR PURPOSE AND NONINFRINGEMENT. IN NO EVENT SHALL THE
//AUTHORS OR COPYRIGHT HOLDERS BE LIABLE FOR ANY CLAIM, DAMAGES OR OTHER
//LIABILITY, WHETHER IN AN ACTION OF CONTRACT, TORT OR OTHERWISE, ARISING FROM,
//OUT OF OR IN CONNECTION WITH THE SOFTWARE OR THE USE OR OTHER DEALINGS IN
//THE SOFTWARE.
///////////////////////////////////////////////////////////////////////////////////////
#include <Wire.h>

byte error, MPU_6050_found, nunchuck_found, lowByte, highByte;
int address;
int nDevices;

void setup()
{
  Wire.begin();
  TWBR = 12;
  Serial.begin(9600);
}

void loop()
{
  Serial.println("Scanning I2C bus...");

  nDevices = 0;
  for(address = 1; address < 127; address++ )
  {
    Wire.beginTransmission(address);
    error = Wire.endTransmission();

    if (error == 0)
    {
      Serial.print("I2C device found at address 0x");
      if (address<16)Serial.print("0");
      Serial.println(address,HEX);
      nDevices++;
      if(address == 0x68 || address == 0x69){
        Serial.println("This could be a MPU-6050");
        Wire.beginTransmission(address);
        Wire.write(0x75);
        Wire.endTransmission();
        Serial.println("Send Who am I request...");
        Wire.requestFrom(address, 1);
        while(Wire.available() < 1);
        lowByte = Wire.read();
        if(lowByte == 0x68){
          Serial.print("Who Am I responce is ok: 0x");
          Serial.println(lowByte, HEX);
        }
        else{
          Serial.print("Wrong Who Am I responce: 0x");
          if (lowByte<16)Serial.print("0");
          Serial.println(lowByte, HEX);
        }
        if(lowByte == 0x68 && address == 0x68){
          MPU_6050_found = 1;
          Serial.println("Starting Gyro....");
          set_gyro_registers();
        }
      }
      if(address == 0x52){
        Serial.println("This could be a Nunchuck");
        Serial.println("Trying to initialise the device...");
        Wire.beginTransmission(0x52);
        Wire.write(0xF0);
        Wire.write(0x55);
        Wire.endTransmission();
        delay(20);
        Wire.beginTransmission(0x52);
        Wire.write(0xFB);
        Wire.write(0x00);
        Wire.endTransmission();
        delay(20);
        Serial.println("Sending joystick data request...");
        Wire.beginTransmission(0x52);
        Wire.write(0x00);
        Wire.endTransmission();
        Wire.requestFrom(0x52,1);
        while(Wire.available() < 1);
        lowByte = Wire.read();
        if(lowByte > 100 && lowByte < 160){
          Serial.print("Data response normal: ");
          Serial.println(lowByte);
          nunchuck_found = 1;
        }
        else{
          Serial.print("Data response is not normal: ");
          Serial.println(lowByte);
        }
      }
    }
    else if (error==4)
    {
      Serial.print("Unknown error at address 0x");
      if (address<16)
        Serial.print("0");
      Serial.println(address,HEX);
    }    
  }
  if (nDevices == 0)
    Serial.println("No I2C devices found\n");
  else
    Serial.println("done\n");
  if(MPU_6050_found){
    Serial.print("Balance value: ");
    Wire.beginTransmission(0x68);
    Wire.write(0x3F);
    Wire.endTransmission();
    Wire.requestFrom(0x68,2);
    Serial.println((Wire.read()<<8|Wire.read())*-1);
    delay(20);
    Serial.println("Printing raw gyro values");
    for(address = 0; address < 20; address++ ){
      Wire.beginTransmission(0x68);
      Wire.write(0x43);
      Wire.endTransmission();
      Wire.requestFrom(0x68,6);
      while(Wire.available() < 6);
      Serial.print("Gyro X = "); 
      Serial.print(Wire.read()<<8|Wire.read());
      Serial.print(" Gyro Y = "); 
      Serial.print(Wire.read()<<8|Wire.read());
      Serial.print(" Gyro Z = "); 
      Serial.println(Wire.read()<<8|Wire.read());
    }
    Serial.println("");
  }
  else Serial.println("No MPU-6050 device found at address 0x68");

  if(nunchuck_found){
    Serial.println("Printing raw Nunchuck values");
    for(address = 0; address < 20; address++ ){ 
      Wire.beginTransmission(0x52);
      Wire.write(0x00);
      Wire.endTransmission();
      Wire.requestFrom(0x52,2);
      while(Wire.available() < 2);
      Serial.print("Joystick X = "); 
      Serial.print(Wire.read());
      Serial.print(" Joystick y = ");
      Serial.println(Wire.read());
      delay(100);
    }
  }
  else Serial.println("No Nunchuck device found at address 0x52");
  while(1);
}

void set_gyro_registers(){
  //Setup the MPU-6050
  Wire.beginTransmission(0x68);                                     //Start communication with the address found during search.
  Wire.write(0x6B);                                                         //We want to write to the PWR_MGMT_1 register (6B hex)
  Wire.write(0x00);                                                         //Set the register bits as 00000000 to activate the gyro
  Wire.endTransmission();                                                   //End the transmission with the gyro.
  
  Wire.beginTransmission(0x68);                                     //Start communication with the address found during search.
  Wire.write(0x1B);                                                         //We want to write to the GYRO_CONFIG register (1B hex)
  Wire.write(0x00);                                                         //Set the register bits as 00000000 (250dps full scale)
  Wire.endTransmission();                                                   //End the transmission with the gyro

  Wire.beginTransmission(0x68);                                     //Start communication with the address found during search.
  Wire.write(0x1C);                                                         //We want to write to the ACCEL_CONFIG register (1A hex)
  Wire.write(0x08);                                                         //Set the register bits as 00001000 (+/- 4g full scale range)
  Wire.endTransmission();                                                   //End the transmission with the gyro

  Wire.beginTransmission(0x68);                                     //Start communication with the address found during search
  Wire.write(0x1A);                                                         //We want to write to the CONFIG register (1A hex)
  Wire.write(0x03);                                                         //Set the register bits as 00000011 (Set Digital Low Pass Filter to ~43Hz)
  Wire.endTransmission();                                                   //End the transmission with the gyro 
}

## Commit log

2020-07-29 3D Models added
    [BatteryPack.stl, BodyPanel.stl, BodyTop.stl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]
2020-07-29 Rename CAD/BatteryPack.stl to CAD/3D Models (Printable)/BatteryPack.stl
    [BatteryPack.stl]
2020-07-29 Rename CAD/3D Models (Printable)/BatteryPack.stl to CAD/3D Models/BatteryPack.stl
    [BatteryPack.stl]
2020-07-29 Rename CAD/BodyPanel.stl to CAD/3D Models/BodyPanel.stl
    [BodyPanel.stl]
2020-07-29 Rename CAD/BodyTop.stl to CAD/3D Models/BodyTop.stl
    [BodyTop.stl]
2020-07-29 Rename CAD/... to CAD/Project Files/...
2020-07-30 Organised files.
    [BatteryPack.stl, BodyPanel.stl, BodyTop.stl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]
2020-07-30 Added Arduino (YABR based) code
